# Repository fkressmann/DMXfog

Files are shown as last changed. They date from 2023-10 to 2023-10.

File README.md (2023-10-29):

# DMXfog

## Idea
This project came along when I got a not-super-new fog machine with just a wired remote with momentary switch. 
It was bugging to always be next to the remote to press it for some seconds to keep a steady-slight fog during an event. 
With lights controlled by DMX, the idea came to build a new remote which can connect to DMX to control to fog machine in a PWM like manner (with two DMX channels indicating frequency and duty cycle).

On top of that a manual timer mode was added in situations where no DMX is available.

The case should be similar to the original remote with its two status LEDs and a momentary push button which I wanted to keep for pure manual operation.

## Features
* Display to show the current mode (DMX or manual) and a countdown to the next action
* DMX mode with two channels (cycle length in seconds and duty cycle in percent)
* Configurable and EEPROM persisted DMX channel
* Manual mode with both parameters set manually
* Auto turn-off when DMX signal is lost
* Parasite power supply trough fog machines current to drive the LEDs which was more than enough

## Hardware
* Arduino Nano (china clone)
* RS485 to TTL converter 
* DC-DC buck converter with LM2596S to step down from fog machine voltage of 12V to Arduino Nano 5V
* 4-digit 7-segment display with TM1637 driver
* some simple 6x6 tactile buttons 

## Build
3D models in sTL format included in the `resources` directory.

How the thing looked like before it come into the box
* RS485 converter on the left, DMX socket not connected
* Remote control on the top
* Arduino Nano in the middle
* buck converter on the bottom
* Transistor on the right to trigger the fog machine (just shorts the 12v supply to the high impedance trigger input of the machine)

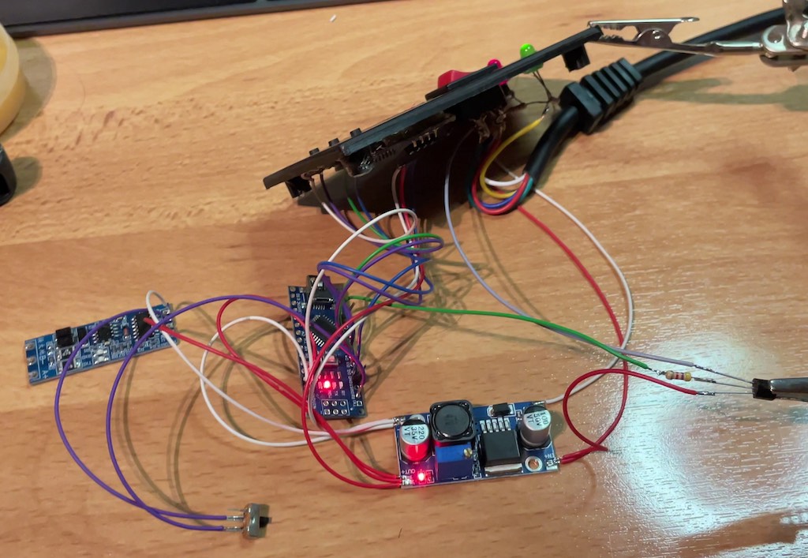
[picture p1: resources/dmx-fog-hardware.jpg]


After everything was nested into the box

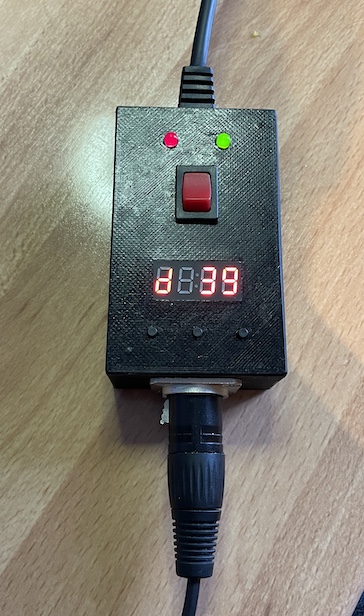
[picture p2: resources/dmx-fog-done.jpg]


## Props to (Libraries)
* [nickgammon/SendOnlySoftwareSerial](https://github.com/nickgammon/SendOnlySoftwareSerial) for debugging cause DMXSerial uses the hardware serial of the Arduino Nano
* [mathertel/DMXSerial](https://registry.platformio.org/libraries/mathertel/DMXSerial) to receive DMX from a RS485 to TTL converter
* [smougenot/TM1637](https://registry.platformio.org/libraries/smougenot/TM1637) as display driver

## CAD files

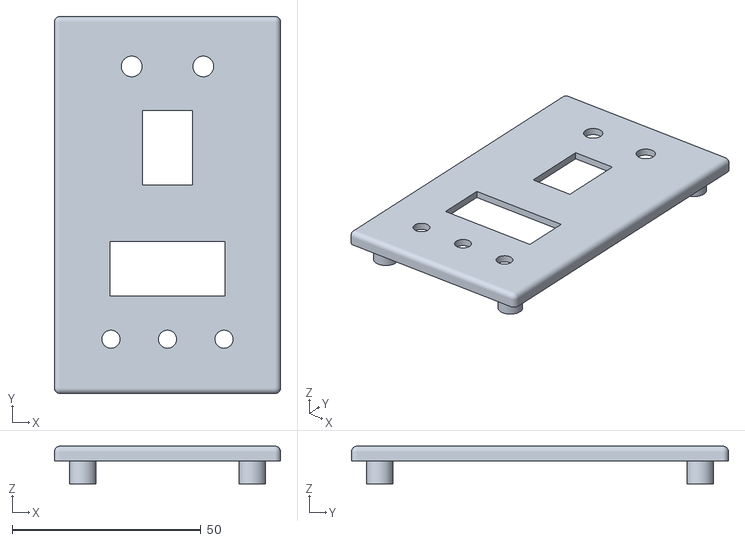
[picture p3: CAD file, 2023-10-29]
resources/dmx-fog-3d-lid.stl
60.0 x 100.0 x 10.0

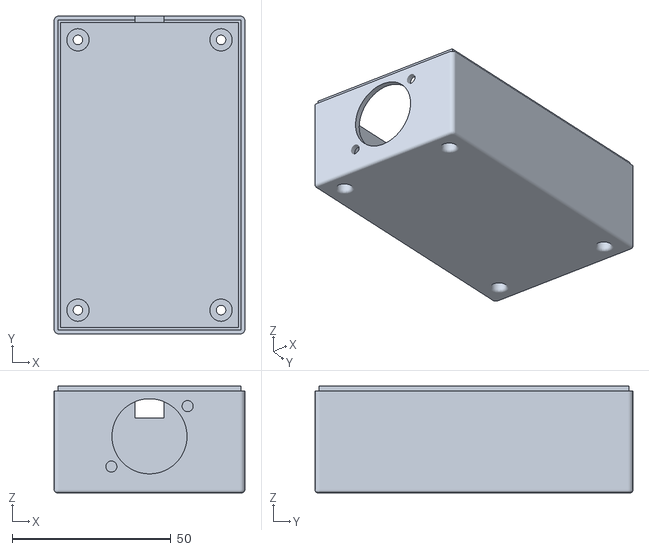
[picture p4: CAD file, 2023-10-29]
resources/dmx-fog-3d-box.stl
60.0 x 100.0 x 33.6

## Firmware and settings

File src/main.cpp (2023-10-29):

//#define SIMULATE_DMX

#include <Arduino.h>
#include <EEPROM.h>
#include <TM1637Display.h>
#include <SendOnlySoftwareSerial.h>

#ifndef SIMULATE_DMX

#include <DMXSerial.h>

#endif

#define DISPLAY_CLK 6
#define DISPLAY_DIO 5
#define SETTINGS_BUTTON 4 // Pin 2 and 3 are usable for interrupts
#define UP_BUTTON 2
#define DOWN_BUTTON 3
#define SERIAL 9
#define TRIGGER 10

int dmxStartChannel = 0;
int dmxDutyCycleChannel;
int dmxFrequencyChannel;
uint8_t currentFrequencySek = 0; // Interval length, seconds, 0-255
uint8_t currentDutyCycleDmxValue; // Duty cycle as DMX value 0-255
float currentDutyCycle = 0; // Duty cycle, decimal, 0-1

unsigned long nextTurnOffTime = 0;
unsigned long currentCycleEnd = 0;

bool dmxMode = true; // false: manual mode
bool needToTurnOff = false;
bool upButtonPressed = false;
bool downButtonPressed = false;

const uint8_t SEG_FOG[] = {SEG_A | SEG_E | SEG_F | SEG_G}; // 'F'
const uint8_t SEG_EDIT_CHANNEL[] = {SEG_A | SEG_F | SEG_E | SEG_D}; // 'C'
const uint8_t SEG_EDIT_MANUAL_CYCLE_DURATION[] = {SEG_A | SEG_F | SEG_C | SEG_D}; // 'S'
const uint8_t SEG_EDIT_MANUAL_DUTY_CYCLE[] = {SEG_A | SEG_F | SEG_B | SEG_G | SEG_E}; // 'P'
const uint8_t SEG_MANUAL_MODE[] = {SEG_A | SEG_G | SEG_E | SEG_C}; // 'M'
const uint8_t SEG_DMX_MODE[] = {SEG_B | SEG_G | SEG_E | SEG_C | SEG_D}; // 'd'
const uint8_t SEG_OFF[] = {SEG_A | SEG_F | SEG_B | SEG_E | SEG_C | SEG_D, // O
                           SEG_A | SEG_E | SEG_F | SEG_G, // F
                           SEG_A | SEG_E | SEG_F | SEG_G}; // F

TM1637Display display(DISPLAY_CLK, DISPLAY_DIO);
SendOnlySoftwareSerial mySerial(SERIAL);

void pwm();

bool readDmx(bool force = false);

void resetDmxUpdated();

void updateChannels() {
    dmxFrequencyChannel = dmxStartChannel;
    dmxDutyCycleChannel = dmxStartChannel + 1;
    mySerial.print("start Channel: ");
    mySerial.println(dmxStartChannel);
    mySerial.print("Frequency Channel: ");
    mySerial.println(dmxFrequencyChannel);
    mySerial.print("Duty Cycle Channel: ");
    mySerial.println(dmxDutyCycleChannel);
}

void isrUp() {
    upButtonPressed = !digitalRead(UP_BUTTON);
}

void isrDown() {
    downButtonPressed = !digitalRead(DOWN_BUTTON);
}

void setup() {
    mySerial.begin(115200);
    mySerial.println("Starting...");
#ifndef SIMULATE_DMX
    DMXSerial.init(DMXReceiver, 12);
#endif
    display.clear();
    display.setBrightness(0x0f);
    pinMode(SETTINGS_BUTTON, INPUT_PULLUP);
    pinMode(UP_BUTTON, INPUT_PULLUP);
    pinMode(DOWN_BUTTON, INPUT_PULLUP);
    attachInterrupt(digitalPinToInterrupt(UP_BUTTON), isrUp, CHANGE);
    attachInterrupt(digitalPinToInterrupt(DOWN_BUTTON), isrDown, CHANGE);
    pinMode(TRIGGER, OUTPUT);
    EEPROM.get(0, dmxStartChannel);
    updateChannels();
}

void setDisplayStatus(const uint8_t segments[]) {
    display.setSegments(segments, 1, 0);
}

void setDisplayStatusAccordingToMode() {
    if (dmxMode) {
        setDisplayStatus(SEG_DMX_MODE);
    } else {
        setDisplayStatus(SEG_MANUAL_MODE);
    }
}

void show3DigitNumber(int number) {
    display.showNumberDec(number, false, 3, 1);
}

int readInputValue(int currentInput, int minValue, int maxValue) {
    float multiplier = 1;
    bool changed = false;
    show3DigitNumber(currentInput);
    while (digitalRead(SETTINGS_BUTTON)) {
        if (currentInput > maxValue) currentInput = minValue;
        if (currentInput < minValue) currentInput = maxValue;
        if (changed) show3DigitNumber(currentInput);
        if (upButtonPressed) {
            currentInput += multiplier;
            multiplier += 0.3;
            changed = true;
        } else if (downButtonPressed) {
            currentInput -= multiplier;
            multiplier += 0.3;
            changed = true;
        } else {
            multiplier = 1;
            changed = false;
        }
        delay(75);
    }
    return currentInput;
}

void editSettings() {
    mySerial.print("Entering Settings for ");
    delay(100);
    while (!digitalRead(SETTINGS_BUTTON)); // Prevent exiting this menu before settings button is released

    if (dmxMode) {
        mySerial.println("DMX mode");
        setDisplayStatus(SEG_EDIT_CHANNEL);
        dmxStartChannel = readInputValue(dmxStartChannel, 1, 512);
        EEPROM.put(0, dmxStartChannel);
        updateChannels();
    } else {
        mySerial.println("manual mode");
        setDisplayStatus(SEG_EDIT_MANUAL_CYCLE_DURATION);
        currentFrequencySek = readInputValue(currentFrequencySek, 0, 240);
        mySerial.print("currentFrequencySek set to: ");
        mySerial.println(currentFrequencySek);
        while (!digitalRead(SETTINGS_BUTTON)); // Prevent exiting this menu before settings button is released
        setDisplayStatus(SEG_EDIT_MANUAL_DUTY_CYCLE);
        int cyclePercentage = readInputValue(currentDutyCycle * 100, 0, 100);
        currentDutyCycle = (float) cyclePercentage / 100;
        mySerial.print("currentDutyCycle set to: ");
        mySerial.println(currentDutyCycle);
    }

    display.clear();
    setDisplayStatusAccordingToMode();
    while (!digitalRead(SETTINGS_BUTTON)); // Prevent exiting this menu before settings button is released
    mySerial.println("leaving settings");
    delay(100);
}

unsigned long lastDmxPacket() {
#ifdef SIMULATE_DMX
    return random(1100);
#else
    return DMXSerial.noDataSince();
#endif
}

#ifndef SIMULATE_DMX

unsigned int readDmxChannel(const int *channel) {
    return DMXSerial.read(*channel);
}

#endif

int readDmxFrequencyChannel() {
#ifdef SIMULATE_DMX
    return random(9, 10);
#else
    return readDmxChannel(&dmxFrequencyChannel);
#endif
}

int readDmxDutyCycleChannel() {
#ifdef SIMULATE_DMX
    return random(128, 129);
#else
    return readDmxChannel(&dmxDutyCycleChannel);
#endif
}

bool dmxUpdated() {
#ifndef SIMULATE_DMX
    return DMXSerial.dataUpdated();
#else
    return random(10); // Probability 10% for not received
#endif
}

void loop() {
    if (digitalRead(SETTINGS_BUTTON) == LOW) {
        digitalWrite(TRIGGER, LOW);
        editSettings();
    }
    bool dmxIsActive = readDmx();

    // Switch to manual mode when no DMX was received for some time
    if (!dmxIsActive && dmxMode) {
        mySerial.println("Switching to manual mode");
        dmxMode = false;
        currentDutyCycle = 0;
        setDisplayStatusAccordingToMode();
        digitalWrite(TRIGGER, LOW);
    }

    // When manual mode is enabled, and we start receiving DMX again, we switch back to DMX mode
    if (dmxIsActive && !dmxMode) {
        mySerial.println("Switching to DMX mode");
        dmxMode = true;
        setDisplayStatusAccordingToMode();
        readDmx(true);
    }

    // Turn output off immediately when one value is set to 0
    if (currentDutyCycle == 0) {
        // Stop fogging if we do and stop loop execution
        digitalWrite(TRIGGER, LOW);
        display.setSegments(SEG_OFF, 3, 1);
        return;
    }

    pwm();
    delay(10);
}

void pwm() {
    unsigned long currentMillis = millis();
    // Check if new cycle needs to be started
    if (currentMillis > currentCycleEnd) {
        mySerial.println("Strating new cycle, fogging");
        nextTurnOffTime = currentMillis + (currentDutyCycle * currentFrequencySek * 1000l);
        currentCycleEnd = currentMillis + (currentFrequencySek * 1000l);
        needToTurnOff = true;
        setDisplayStatus(SEG_FOG);
        digitalWrite(TRIGGER, HIGH);
    }
    // Check if trigger needs to be turned off
    if (needToTurnOff && currentMillis > nextTurnOffTime) {
        mySerial.println("Fogging stop");
        setDisplayStatusAccordingToMode();
        digitalWrite(TRIGGER, LOW);
        needToTurnOff = false;
    }

    // Update display countdown
    int sekLeft;
    if (needToTurnOff) {
        sekLeft = (nextTurnOffTime - currentMillis) / 1000 + 1;
    } else {
        sekLeft = (currentCycleEnd - currentMillis) / 1000 + 1;
    }
    show3DigitNumber(sekLeft);
}

bool readDmx(bool force) {
    unsigned long lastPacket = lastDmxPacket();
    if (lastPacket < 5000) {
        if (dmxUpdated() || force) {
            // Check for frequency changes
            unsigned int newDmxValueFrequency = readDmxFrequencyChannel();
            if (newDmxValueFrequency != currentFrequencySek) {
                mySerial.print("New DMX frequency: ");
                mySerial.println(newDmxValueFrequency);
                currentFrequencySek = newDmxValueFrequency;
                // If interval length changed, reset current running interval and start over
                currentCycleEnd = 0;
                nextTurnOffTime = 0;
                needToTurnOff = false;
            }

            // Check for duty cycle changes
            unsigned int newDmxValueDutyCycle = readDmxDutyCycleChannel();
            if ((newDmxValueDutyCycle != currentDutyCycleDmxValue) || force) {
                mySerial.print("New DMX duty cycle: ");
                mySerial.println(newDmxValueDutyCycle);
                currentDutyCycleDmxValue = newDmxValueDutyCycle;
                currentDutyCycle = (float) newDmxValueDutyCycle / 255;
            }
            resetDmxUpdated();
        }
        return true;
    } else {
        return false;
    }
}

void resetDmxUpdated() {
#ifndef SIMULATE_DMX
    DMXSerial.resetUpdated();
#endif
}

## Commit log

2023-10-14 Basic PWM like implementation but for 1-255 sek intervals
2023-10-14 Add basic three button menu with display
2023-10-15 Fix display / settings
    [main.cpp]
2023-10-15 Switch to send only serial for debugging with DMX connected (need the hardware serial port)
2023-10-16 Reset DMX updated status every time we change settings
    [main.cpp]
2023-10-16 - Bugfix logic doesn't recover from lost DMX signal - Fix cycle calculation for longer periods (50+ sek) which needs to be done as longs not as ints
    [main.cpp]
2023-10-22 Add manual mode when no DMX input is received. Still untested: switching back to DMX mode
2023-10-22 Indicate when timer is OFF
2023-10-29 Fix misunderstanding of how DMXSerial.resetUpdated() is supposed to work and thus fix bug that after reconnecting DMX fog cycle did not start again if channel values were not chnaged
    [main.cpp]
2023-10-29 Adding readme and other resources
    [dmx-fog-3d-box.stl, dmx-fog-3d-lid.stl]
